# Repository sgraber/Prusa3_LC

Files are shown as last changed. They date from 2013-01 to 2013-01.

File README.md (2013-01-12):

Prusa3_LC
=========

Laser cut files for the Prusa i3 printer frame - both Standard Single Sheet and Mini versions: https://github.com/josefprusa/Prusa3/

Published under GPL v3, same as the Prusa 3.

The goal of this revision is to allow people to use frame material that is less rigid than the 6mm aluminum, which is specified for the Single Sheet Frame Prusa i3 Printer (http://reprap.org/wiki/Prusa_i3#Single_Sheet_Frame) and have it laser cut instead of water jet cut. Laser cutters are more accessible for people either at their local makerspace or at local laser cutting businesses. Laser cut material is also less expensive and people can source different frame colors and materials, such as 5mm birch plywood, 6mm double-faced melamine, and 1/4" acrylic.

To achieve this goal, two angular braces are designed and added to the bill of materials and the stock Prusa i3 Single Sheet Frame is slightly modified to accept these braces. A major goal of this revision is to keep the Prusa i3 frame as stock as possible so that people can continue to print and use Josef Prusa's i3 parts from his Github repository: https://github.com/josefprusa/Prusa3/ In this release, the frame dimensions were not changed at all. The only additional items added to the i3 bill of materials are the two laser cut braces and six 25mm/1-inch M3/6-32 SAE screws and washers.

This frame was designed for use with 6mm-thick material. Thicknesses less than or greater than 6mm will require the brace tab lengths to be decreased/increased and the square tab-accepting holes in the Prusa i3 frame to be decreased/increased accordingly. I have found that oversizing the tab-accepting holes by 0.2mm works but each laser cutter is slightly different and may require adjustments different than this.

More photos are found on my photostream at Flickr: http://www.flickr.com/photos/sbgraber/8351936888/in/photostream/

This repository contains two different frame sizes: the Standard Single Sheet Frame and the Mini Single Sheet Frame. The Standard frame is for 200mm (8") square heated beds. The Mini frame is for 100mm (4") square print beds, and is a smaller version of the Prusa i3.

Changed and New Parts
=====================

Changes to the stock Prusa i3 frame:

* Screw hole size increased from 2.5mm to 3.5mm to allow for either 3mm or 6-32 SAE screws
* Added square tab holes for braces
* Increased bottom 8mm circular holes to 16mm oblong holes to allow pre-wired motor connectors to fit through
* Moved RAMPS 1.4 mounting holes to the braces
* Added "i3" text to top of frame
* removed two heat sink for extruder motor as wood / acrylic makes for poor heat sink material
* removed y-alignment tool and associated holes in frame as the new braces take care of this

New braces (2):

* Measure 370mm tall x 178mm wide (14.6" x 7")
* Oblong holes in brace bottom allow for pre-wired motor (and other) connectors to fit through
* Mounting holes for both RAMPS 1.4 and RAMBo one one brace (Sanguinololu and RUMBA holes on the other brace forthtcoming)
* 80mm x 8.8mm slot in bottom ties into the top-back y-axis threaded rod using four washers and nuts and an extended y-axis threaded rod
* Nut traps accept either M3 or 6-32 hardware (Nyloc nuts, 25mm / 1 inch screws)

Changes to the stock Prusa i3 Mini frame:

* Added square tab holes for braces
* Moved RAMPS 1.4 mounting holes to the braces
* Removed y-alignment tool and associated holes in frame as the new braces take care of this
* Beefed up perimeter of y-carriage by 2mm
* Swapped out LM8UU printed bearing holders for LM8UU mounting holes, like the Standard Prusa i3 y-carriage

New Mini braces (2):

* Measure 273mm tall x 100mm wide (10.75" x 4")
* RAMPS 1.4 mounting holes moved from frame to braces
* 54mm x 8.8mm slit in bottom ties into the top-back y-axis threaded rod using four washers and nuts and an extended y-axis threaded rod
* * Nut traps accept either M3 or 6-32 hardware (Nyloc nuts, 25mm / 1 inch screws)

How to obtain laser cut frames
==============================

I have provided three file types for people to use when laser cutting: dxf, eps, and pdf. Your local makerspace or laser cutting business should be able to utilize one of these three file formats to cut your frame and braces for you. "frame-6mm-colored-lines.dxf" and "frame-6mm-mini-colored-lines.dxf" has the lines colored for easier laser cutting: green=raster, yellow=1st cut, orange=2nd cut, brown=3rd cut, red=last cut.

If you would prefer to purchase one of these frames and associated braces online, I will soon provide these parts on Ebay along with my printed parts, which conform to the latest versions found at https://github.com/josefprusa/Prusa3/ branch. This way you can source most of what you need from one place: http://myworld.ebay.com/sbgraber

I worked with the guys at SeeMeCNC during development of this frame revision and they are also providing the frames for purchase from their website: http://shop.seemecnc.com/  These guys are great to work with and I highly recommend them and their products.

Assembly
========

Materials:

* Frame (1)
* Brace (2)
* M3 / 6-32 SAE screw, 25mm / 1-inch long (6)
* M3 / 6-32 SAE washers (6)
* M3 / 6-32 SAE nut / nyloc (6)

Slide the tabbed braces into the frame. Slide a washer onto an M3/6-32 SAE screw and insert the screw into each nut trap hole. Use either a standard or nyloc M3/6-32 SAE nut and screw tight.

Assemble the remainder of the printer per the instructions in Prusa's repository: https://github.com/josefprusa/Prusa3/blob/master/doc/manual.txt

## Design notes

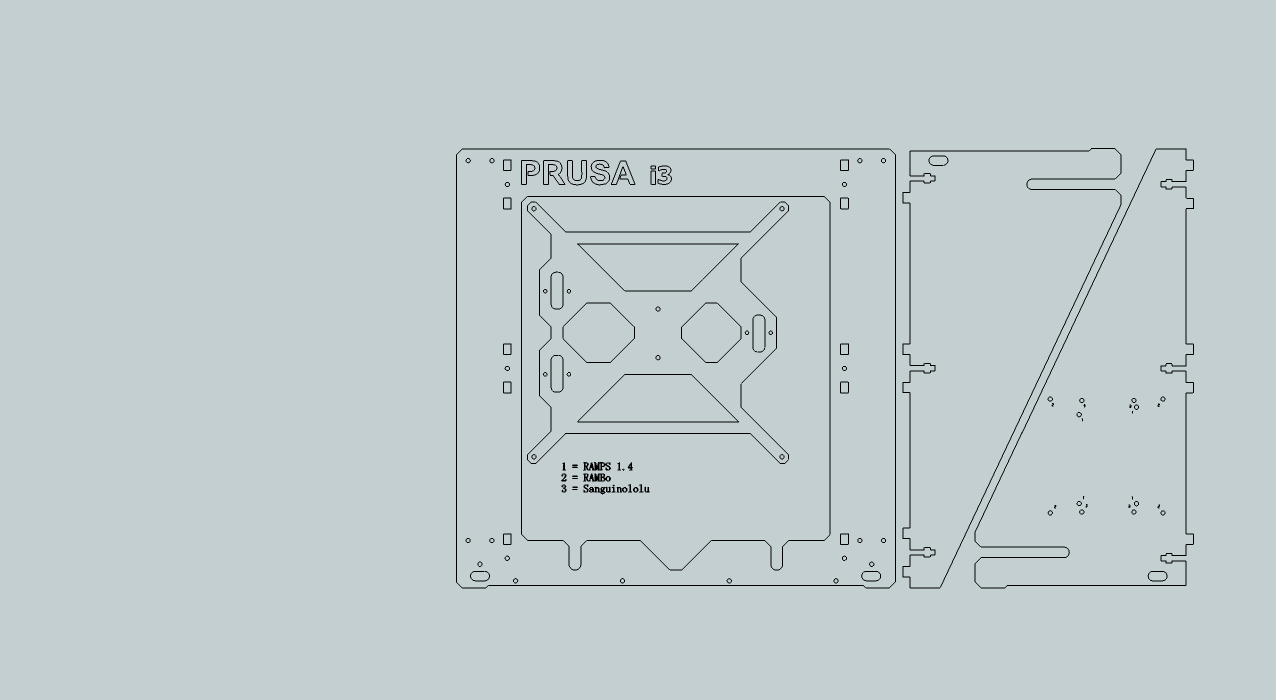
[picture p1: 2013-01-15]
frame-6mm.png

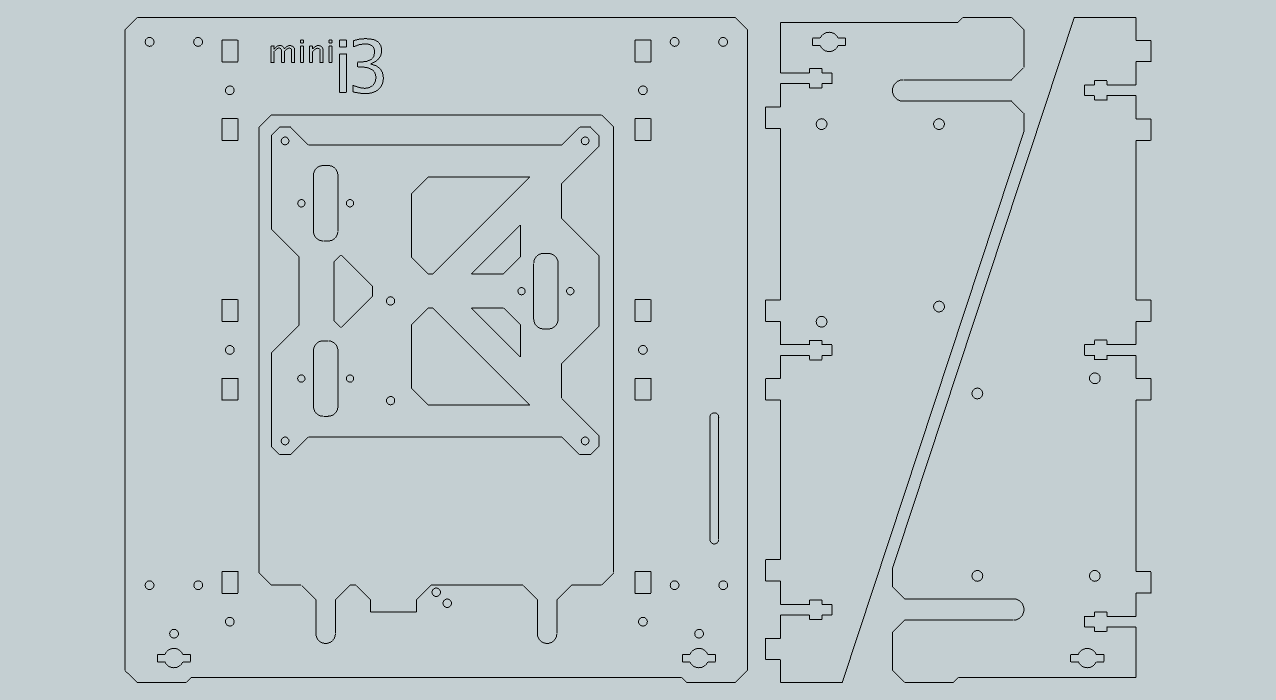
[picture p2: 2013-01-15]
frame-6mm-mini.png

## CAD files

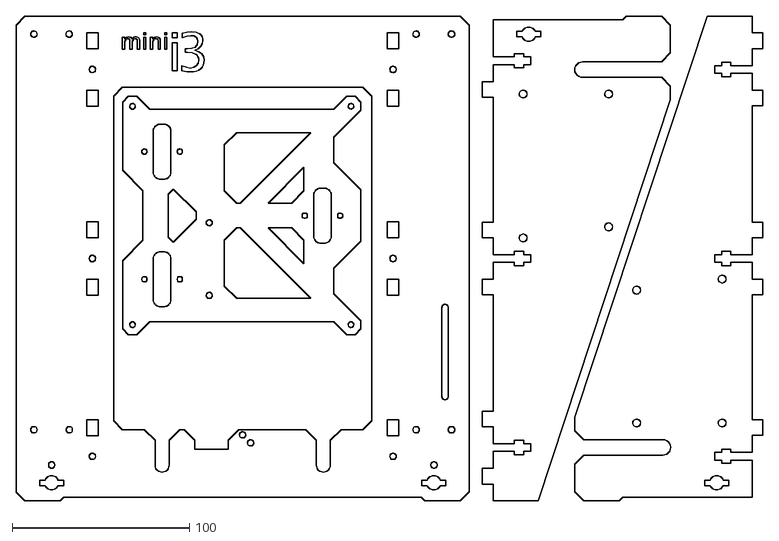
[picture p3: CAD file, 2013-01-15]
frame-6mm-mini.dxf
421.4 x 273.3

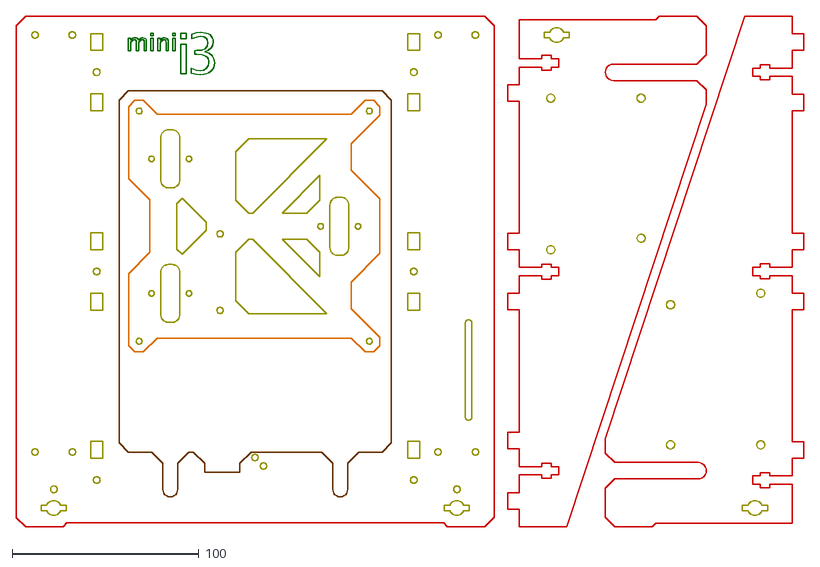
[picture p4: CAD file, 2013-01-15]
frame-6mm-mini-colored-lines.dxf
421.4 x 273.3

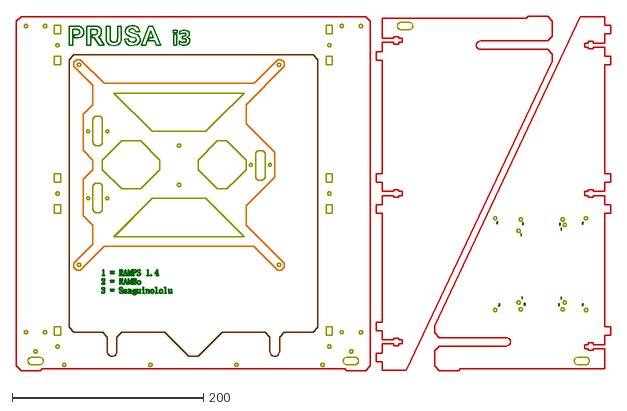
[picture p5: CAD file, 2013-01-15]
frame-6mm-colored-lines.dxf
620.9 x 370.1

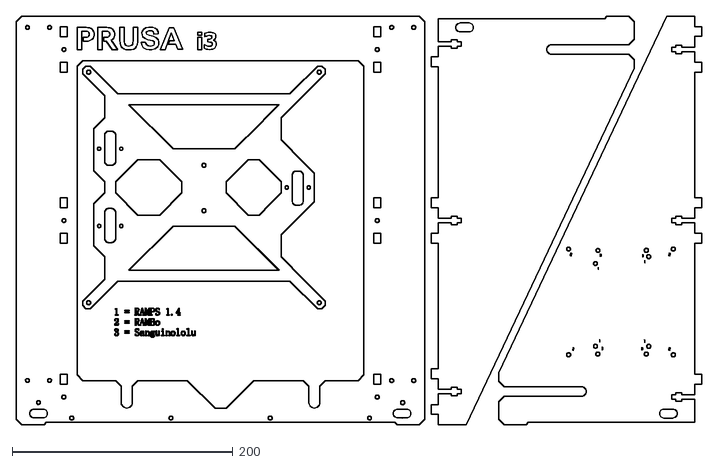
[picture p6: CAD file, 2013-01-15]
frame-6mm.dxf
620.9 x 370.1

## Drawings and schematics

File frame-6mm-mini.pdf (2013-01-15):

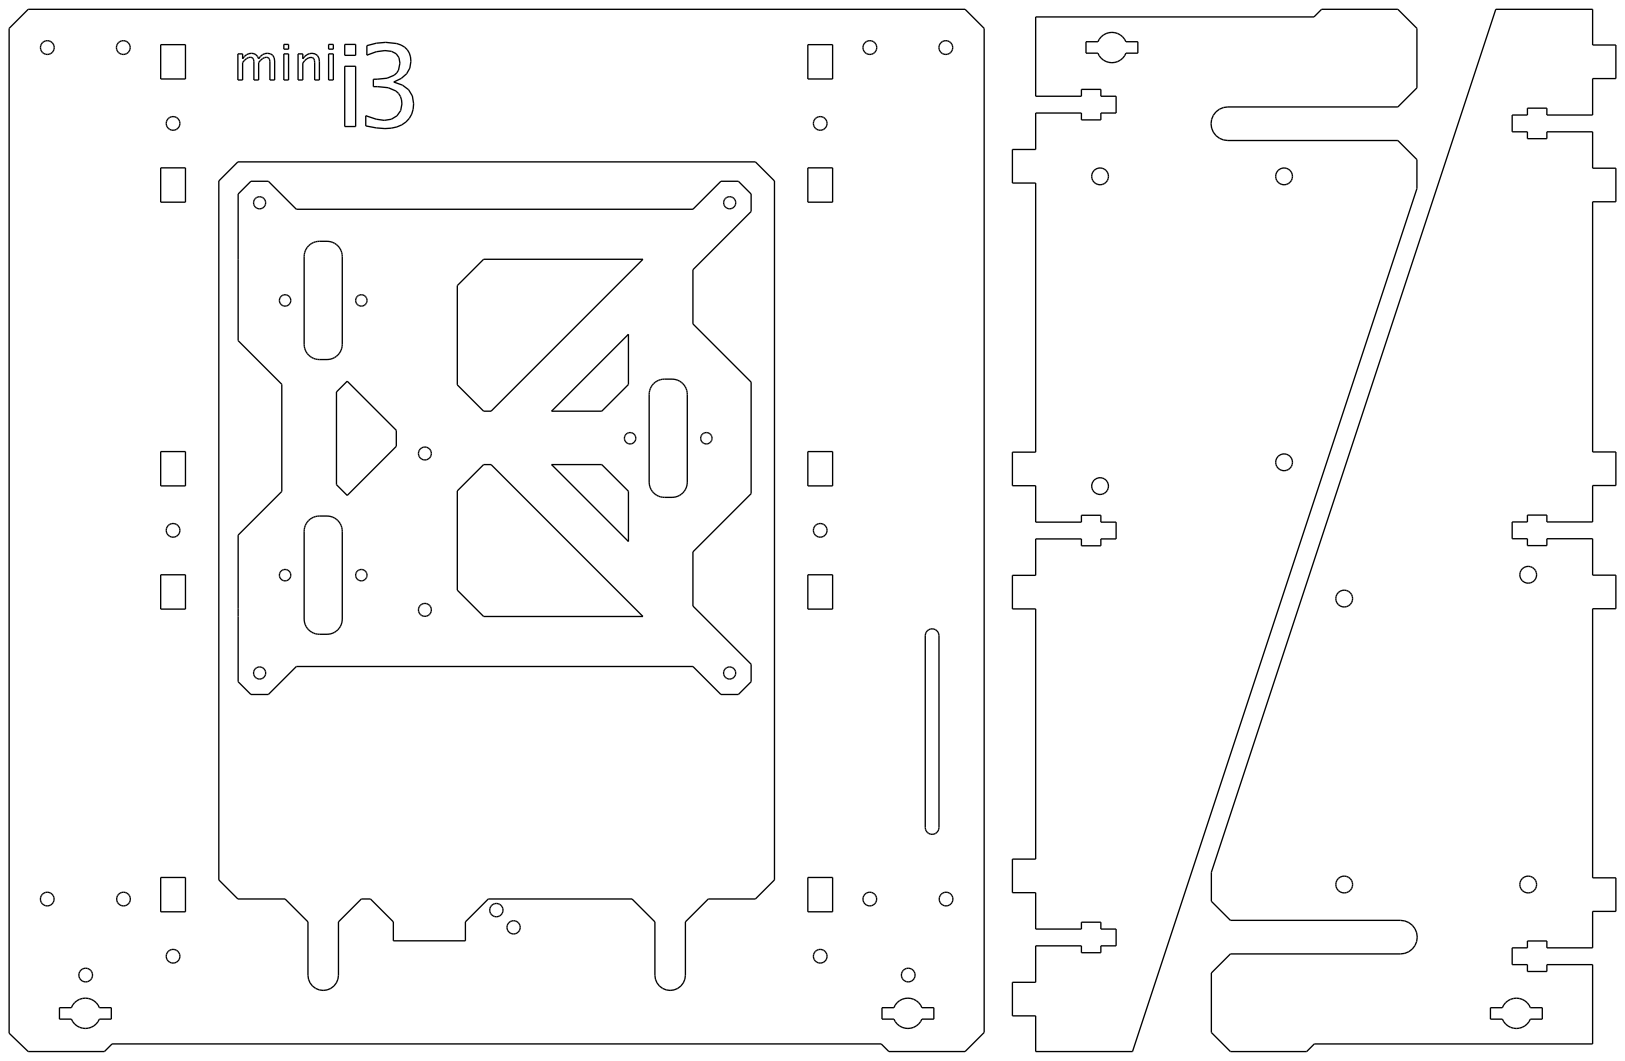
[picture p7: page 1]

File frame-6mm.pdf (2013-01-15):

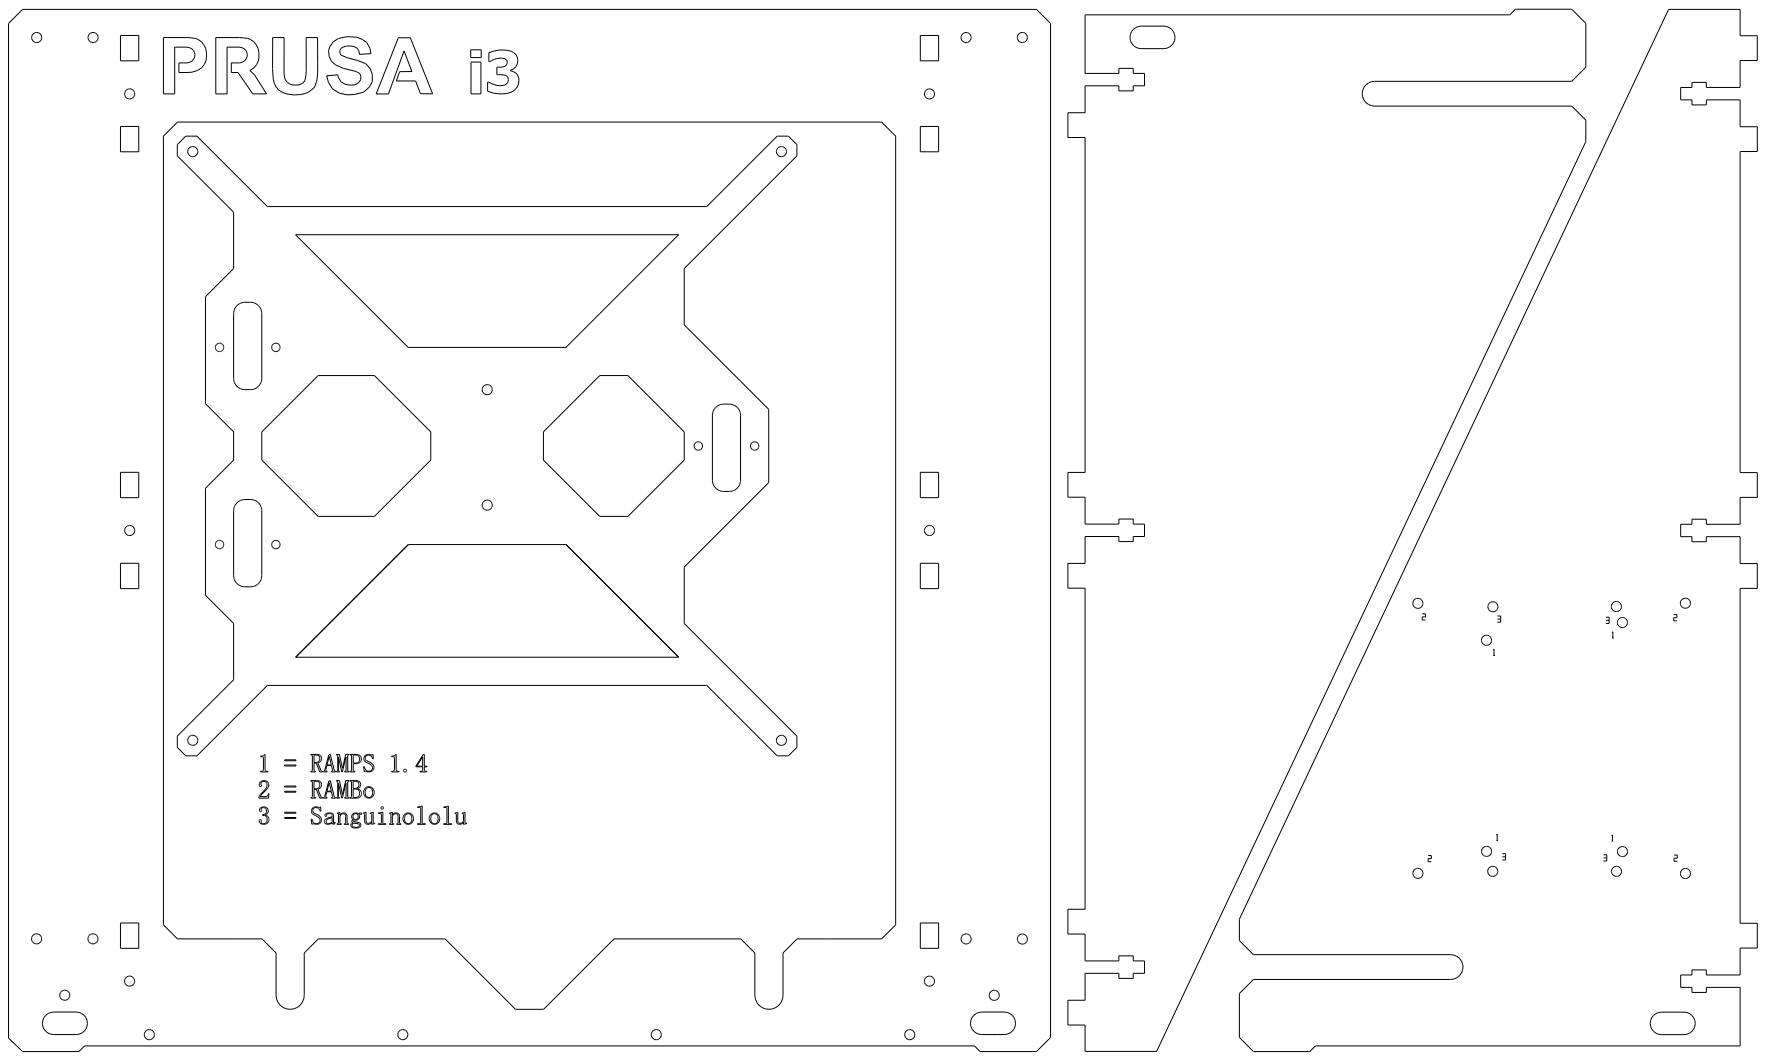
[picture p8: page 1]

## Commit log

2013-01-06 removed bottom-right brace holes from frame
    no need for them any longer since this design uses braces for stability
    and y-alignment.
    [frame-6mm.dxf]
2013-01-06 removed motor heat sinks and y-alignment tool
    neither are needed. wood / acrylic makes for a poor heat sink and the
    braces are now used for y-alignment.
    [frame-6mm.dxf]
2013-01-06 updated with information on obtaining a laser cut frame
2013-01-06 added sanguinololu mounting holes
    [frame-6mm.dxf]
2013-01-06 moved "i3" text a bit to put it level with the PRUSA text
    [frame-6mm.dxf]
2013-01-06 added printrboard holes
    [frame-6mm.dxf]
2013-01-06 fixed lm8uu y-carriage hole spacing
    Took center to center spacing from 30mm to 28mm as lm8uu y-carriage
    parts were not lining up with holes properly.
    [frame-6mm.dxf]
2013-01-06 fixed heated bed hole spacing
    hole spacing was slightly off. now screw holes are properly aligned at
    209mm on the sides and 295.6mm on the diagonals
    [frame-6mm.dxf]
2013-01-09 lm8uu's mounted to y-carriage, zip tie holes along z bottom, removed motor mounts
    Latest revision obsoletes three LM8UU plastic parts on the underside of
    the y-carriage and has them directly mounted to the y-carriage with zip
    ties. Four holes added to the bottom of the frame for holding wires in
    place with zip ties. Removed Printrboard mount holes. Removed motor
    mounts.
    [frame-6mm.dxf]
2013-01-09 cleanup of two missed lines on y-carriage
    [frame-6mm.dxf]
2013-01-09 initial commit
    colored lines for easier laser cutting
    [frame-6mm-colored-lines.dxf]
2013-01-09 Updated with colored laser cut lines in .dxf.
2013-01-09 cleaned up jaggies
    [frame-6mm-colored-lines.dxf, frame-6mm.dxf]
2013-01-11 updated frame for 10mm threaded rods
    [frame-6mm-colored-lines.dxf, frame-6mm.dxf]
2013-01-11 prusa-mini frame, initial import
    [frame-6mm-mini.dxf]
2013-01-12 colored for laser cutting order. initial commit.
    [frame-6mm-mini-colored-lines.dxf]
2013-01-12 updated with Prusa Mini frame info.
2013-01-15 fixed problem where y-carriage impacts the frame
    mounting the lm8uu's to the y-carriage dropped the y-carriage enough
    that through screws on the corners of the heated bed would hit the
    frame. the frame edge was dropped by 10mm to resolve the problem.
    [frame-6mm-colored-lines.dxf, frame-6mm-mini-colored-lines.dxf, frame-6mm-mini.dxf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]
